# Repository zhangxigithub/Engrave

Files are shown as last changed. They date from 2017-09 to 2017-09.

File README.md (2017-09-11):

# README #

包含所有代码和设计图

### 目录说明 ###

* 设计图 : 包含3D模型 和 autocad零件图
* Mac App : 上位机程序，解析SVG，控制下位机
* Arduino App : 下位机，控制刀刀头移动

### module.cpp ###

* Motor 控制每一个轴的电机
* Laser 控制激光通断
* Joystick 接收摇杆的信号，手动控制电机移动

* 上位机下位机通信采用JDY-80蓝牙模块，Bluetooth 4.0, 无需配对，上位机查找到设备后，直接发送指令
* A4988驱动步进电机
* 考虑到功率不大，只需要S8550三极管 控制激光头和散热风扇通断。

### 计划实现 ###
* 解析SVG，画直线和折线（优先）
* 圆、椭圆
* 位图(256级别灰度) 处理图像，控制arduino逐行扫描，一次发送一行数据和方向，S形扫描

### 开发日志 ###
2017 
* 8.30  淘宝购买激光头、arduino板子、步进电机等
* 8.31  设计外壳，和组装方式，淘宝激光切割亚克力外壳(96元)
* 9.1   购买继电器、三极管等元件
* 9.2   编写驱动步进电机程序，接错线了，烧了两个A4988芯片。
* 9.4   亚克力外壳送到，开始组装外壳和滑轨，有一片亚克力开孔开错了位置，自己重新打孔。
* 9.5   极管到了，用三极管做开关，板载5V给激光头供电，arduino烧了。
* 9.6   继电器到了，用继电器做开关，板载5V给激光头供电，arduino+A4988烧了。激光头改成单独供电，正常。
* 9.7   等新的A4988芯片，今天写上位机程序，实现位图的解析。
* 9.9   A4988来了，控制电路部分基本完成，手动画了一个2.5厘米啊的正方形。
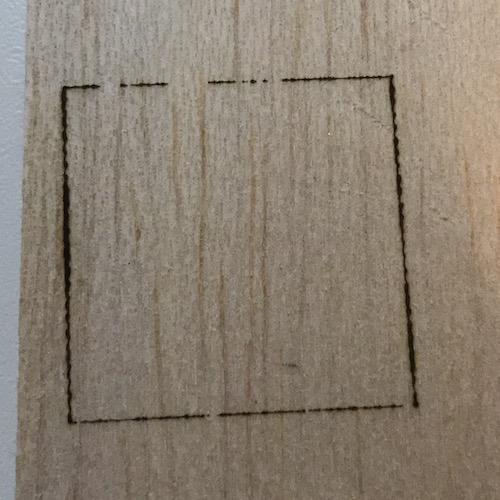
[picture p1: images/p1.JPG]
2.5cm rectangle

* 9.10  用L298N控制输出电压，控制激光头得功率，结果L298N一路输出有问题，5V的输入有将近2V的压降，花了很长时间才确定是模块本身的问题，该用另外一路输出就没有问题了。
* 9.11  继续写上位机位图解析，并控制下位机移动。

### 脑子进水 ###
* 焊板子翻过来后针脚记错了，烧了两个A4988驱动
* 激光头到了，可是太亮，不敢直接看，不好调焦，问了淘宝卖家，卖家说点根烟，激光照到烟雾上，可以清晰的看到焦点的位置。我又不抽烟，还能跑到公司楼下看看哪个大哥在抽烟，然后上去说：大哥，你先别动，我调个焦。后来跟我媳妇说别的事的时候，无意间问了句你知道LED怎么连么。她说不连上就行，我说那就烧了，得串个电阻。过了一个小时我突然意识到，对啊，激光头功率太大，串个电阻减小功率就不这么亮了。
* 把激光头和散热风扇两根电源绑在一起，为了测试分别是哪根，直接接到12V电源上，第一个测试的是风扇，转。又把激光头也接上试试，烧了.
* 不知道为什么...arduino板子烧了，还好用的是便宜的山寨板，不知道和这个有没有关系，明天把开关从三极管改成继电器试试吧
* 改了继电器了 还是又烧了一块板子 什么情况啊。。下回把激光改成单独供电
* 
*

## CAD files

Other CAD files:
设计图/零件导出.dwg
设计图/雕刻机.dwg

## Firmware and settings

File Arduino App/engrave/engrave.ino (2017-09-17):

#include <SoftwareSerial.h>

#include "module.cpp"


Motor motorX(2,3);
Motor motorY(4,5);
Laser laser(6);

SoftwareSerial ble(9,8);

void setup() {
  //Serial.begin(9600);
  //Serial.println("start");
  ble.begin(9600);
  
  digitalWrite(12,HIGH);
  
}



void move(long x,long y,bool enableLaser)
{
    if(enableLaser)
    {
      laser.on();
      ble.println("open laser");
    }

    //total 20000*20000

    long dX = x - motorX.position;
    long dY = y - motorY.position;
    float m = abs(float(dY)/float(dX));
    ble.println("dX : "+String(dX) +" dY : "+String(dY)+" m : "+String(m));
    motorX.changeDirection((dX > 0));
    motorY.changeDirection((dY > 0));
    
    if (m <= 1)
    {
      float detal = 0;
      for(long i = 0; i < abs(dX); i++)
      {
        //ble.print("x move");
        motorX.step();
        detal += m;
        if (detal >= 0.5)
        {
          //ble.print("y move");
          motorY.step();
          detal -= 1;
        }else
        {
        }
      } 
    }else
    {
      float detal = 0;
      for(long i = 0; i < abs(dY); i++)
      {
        //ble.print("y move");
        motorY.step();
        detal += m;
        if (detal >= 0.5)
        {
          //ble.print("x move");
          motorX.step();
          detal -= 1;
        }else
        {
        }
      } 
    }

    if(enableLaser)
    {
      laser.off();
      ble.println("close laser");
    }
    ble.println("move finish x:"+String(motorX.position)+" y : "+String(motorX.position));
}
String op = "";

void loop() {
 if( ble.available() > 0 ){
    op += char(ble.read());
    delay(3);
  }
  if(op.endsWith("#") == false)
  {
    return;
  }



  String action = op.substring(0,1);


  if (action == "m")
  {
    ble.println(op);
    int x      = op.substring(1,6).toInt();
    int y      = op.substring(6,11).toInt();
    bool laser = op.substring(11,12).toInt() == 1;
    
    ble.println(x);
    ble.println(y);

    move(x,y,laser);
    ble.println("svgfinish");
  }
  else if (action == "x")
  {
    ble.println(op);
    bool direction = op.substring(1,2) == "1";
    motorX.changeDirection(direction);

    for(int i=0;i<5000;i++)
    {
      motorX.step();
    }
    motorX.duration = 1000;
    delay(10);
  }else if (action == "y")
  {
    ble.println(op);
    bool direction = op.substring(1,2) == "0";
    motorY.changeDirection(direction);
    for(int i=0;i<5000;i++)
    {
      motorY.step();
    }
    motorY.duration = 1000;
    delay(10);
  }else if (action == "l")
  {
    ble.println(op);
    int l = op.substring(1,4).toInt();
    laser.light(l);
  }else if (action == "r")
  { 
    ble.println("r start");
    bool d = op.substring(1,2) == "1";
    motorX.changeDirection(d);

    
    for(int i=2;i< 52;i++)
    {
      int value   = op.substring(i,i+1).toInt();
      if (value > 3)
      {
        laser.on();
        delay(100);
      }else
      {
        laser.off();
      }
      
      for(int j=0;j< 30;j++){ motorX.step(); }
      ble.println("x move");
    }
    for(int j=0;j< 30;j++){ motorY.step(); }
    laser.off();
    ble.println("linefinish");
  } if (action == "n")
  {
    motorY.changeDirection(true);
    for(int j=0;j< 20;j++){ motorY.step(); }
  }

 op = "";
}

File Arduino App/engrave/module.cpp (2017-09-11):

#include <Arduino.h>

class Motor
{
    public:
    Motor(int d,int s):directionPort(d),stepPort(s){
    pinMode(d,OUTPUT);
    pinMode(s,OUTPUT);
  }

  int stepPort;
  int directionPort;
  int position = 0;
  bool direction = false;
  int duration = 650;
  
  void changeDirection(bool d)
  {
    direction = d;
    digitalWrite(directionPort, d);
  }

  void step()
  {
    position += direction ? 1 : -1;
    
//    if ((position <= 0) || (position >= 10000))
//    {
//      return;
//    }
    
    digitalWrite(stepPort, HIGH);
    delayMicroseconds(duration);
    digitalWrite(stepPort, LOW);
    delayMicroseconds(duration);

    
  }
};

class Laser
{
    public:
    Laser(){}
    Laser(int p):port(p){
    pinMode(p,OUTPUT);
    analogWrite(port,0);
  }

  int port;

  void light(int l)
  {
    analogWrite(port,l);
  }
  void on()
  {
    light(255);
  }
  void off()
  {
    light(0);
  }

};
class Joystick
{
  public:
    Joystick(int x,int y):xPort(x),yPort(y){
    pinMode(x,INPUT);
    pinMode(y,INPUT);
  }
  int xPort;
  int yPort;

  int moveAction()
  {
    int x = analogRead(A4);
    int y = analogRead(A5);
    if(x < 100) {return 1;}
    if(x > 900) {return 2;}
    if(y < 100) {return 3;}
    if(y < 900) {return 4;}
    return 0;
  }
};

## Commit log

2017-09-04 基本完成控制XY电机走直线
    [雕刻机.dwg, 零件导出.dwg]
2017-09-04 预留控制XY按钮
2017-09-05 增加module.cpp
2017-09-05 增加readme
2017-09-05 整理代码
2017-09-05 增加蓝牙通信
2017-09-05 板子烧了
2017-09-06 又烧了一块板子
2017-09-06 增加上位机读取图片的代码 未完成
2017-09-07 预留逐行扫描
2017-09-15 优化点阵雕刻
2017-09-17 优化svg雕刻
